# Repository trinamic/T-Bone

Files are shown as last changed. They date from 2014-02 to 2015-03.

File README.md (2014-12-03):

T-Bone
======
Electronic for up to 5 axes DIY desktop manufacturing platforms

LICENSE Files
=============
"LICENSE_HW" --> Attribution-ShareAlike 4.0 International license effective for the hardware part
"LICENSE_SW" --> agpl-3.0 license effective for the software part

"Software/ArduinoClient" Folder
===============================
The ArduinoClient folder  contains the Arduino software.

"Documentation/SoftwareDocumentation.pdf" File
==============================================
Documentation for the implemented protocol to communicate with the T-Bone via the UART interface.

"Documentation/T-bone_command_documentation.txt" File
=====================================================
Example file for the communication between Beagle Bone Black and the T-Bone (Arduino Leonardo)

Arduino Leonardo Pinout
=======================
Adapted from pins.h in the Arduino software.

Arduino Pin – Atmel Pin & function - connection

    D0 - PD2, RXD1/INT2 - Serial BeagleBone (UART1_TXD)
    D1 - PD3 TXD1/INT3 - Serial BeagleBone (UART1_RXD)
    D2 - PD1 SDA SDA/INT1 - Interrupt 4361 Nr.2
    D3# - PD0 PWM8/SCL OC0B/SCL/INT0 - Interrupt 4361 Nr.1
    D4 - A6 - PD4 ADC8 - CS 4361 Nr. 1
    D5# - PC6 ??? OC3A/#OC4A - PWM3, Fan
    D6# A7 - PD7 FastPWM #OC4D/ADC10 - CS 5031 Nr. 3
    D7 - PE6 INT6/AIN0 - Interrupt 4361 Nr.3
    D8 A8 - PB4 ADC11/PCINT4 - Interrupt 5041
    D9# A9 - PB5 PWM16 OC1A/#OC4B/ADC12/PCINT5 - PWM 1
    D10# A10 - PB6 PWM16 OC1B/0c4B/ADC13/PCINT6 - PWM 2
    D11# - PB7 PWM8/16 0C0A/OC1C/#RTS/PCINT7 - CS 5041
    D12 A11 - PD6 T1/#OC4D/ADC9 - CS 4361 Nr. 2
    D13# - PC7 PWM10 CLK0/OC4A - clock output do not use, never!
    A0 - D18 PF7 ADC7 - Temperature Sensor 1
    A1 - D19 PF6 ADC6 - Temperature Sensor 2
    A2 - D20 PF5 ADC5 - Temperature Sensor 3
    A3 - D21 PF4 ADC4 - Start Signal
    A4 - D22 PF1 ADC1 - Current PWM 1
    A5 - D23 PF0 ADC0 - Current PWM 2
    MISO - D14 PB3 MISO,PCINT3 - MISO
    SCK - D15 PB1 SCK,PCINT1 - SCK
    MOSI - D16 PB2 MOSI,PCINT2 - MOSI
    SS - D17 PB0 RXLED,SS/PCINT0 - RX LED
    TXLED - PD5 . TX LED
    HWB - PE2 HWB - Reset for motion drivers

"Software/ArduinoLibraries" Folder
==================================
This folder contains the used Arduino Libraries needed to compile the code.
!!Attention!!
The used libraries are standard ones, BUT customized. So be sure to use these!
!!Attention!!

For information on installing libraries, see: http://arduino.cc/en/Guide/Libraries

"Software/t_bone_server" Folder
===============================
This folder contains the software running on the Beagle Bone Black for the Deluxe version.

It's prepared to run a 3D-Printer Hardware. But can be customized to control different kind of desktop manufacturing platforms.

"Hardware/T-Bone Folder"
========================
Contains schematic and board design of the latest version of the T-Bone HW

"Hardware/Programming board" Folder
===================================
Contains schematic of a programming board adapter

"Hardware/BBQ" Folder
=====================
Contains schematic and board design for BBQ breakout board to evaluate TMC chipsets

"Hardware/TMC2100" Folder
=========================
Contains startup instructions for TMC2100 breakout board and schematics + board design

LJ

The T-Bone Team
2014

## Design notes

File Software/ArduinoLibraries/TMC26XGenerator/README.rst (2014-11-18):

Arduino TMC26X Stepper Motor Controller Library
===============================================

License
-------

TMC26XStepper.cpp - - TMC 260/261/262 Stepper library for Wiring/Arduino
 
based on the stepper library by Tom Igoe, et. al.
 
Copyright (c) 2011, Interactive Matter, Marcus Nowotny
 
Permission is hereby granted, free of charge, to any person obtaining a copy
of this software and associated documentation files (the "Software"), to deal
in the Software without restriction, including without limitation the rights
to use, copy, modify, merge, publish, distribute, sublicense, and/or sell
copies of the Software, and to permit persons to whom the Software is
furnished to do so, subject to the following conditions:
 
The above copyright notice and this permission notice shall be included in
all copies or substantial portions of the Software.
 
THE SOFTWARE IS PROVIDED "AS IS", WITHOUT WARRANTY OF ANY KIND, EXPRESS OR
IMPLIED, INCLUDING BUT NOT LIMITED TO THE WARRANTIES OF MERCHANTABILITY,
FITNESS FOR A PARTICULAR PURPOSE AND NONINFRINGEMENT. IN NO EVENT SHALL THE
AUTHORS OR COPYRIGHT HOLDERS BE LIABLE FOR ANY CLAIM, DAMAGES OR OTHER
LIABILITY, WHETHER IN AN ACTION OF CONTRACT, TORT OR OTHERWISE, ARISING FROM,
OUT OF OR IN CONNECTION WITH THE SOFTWARE OR THE USE OR OTHER DEALINGS IN
THE SOFTWARE.

About
-----

The TMC26X is a stepper motor controller for bipolar stepper motors. From the trinamic web site:

 The TMC262 is the first energy efficient high current high precision microstepping driver 
 IC for bipolar stepper motors. The unique high resolution sensorless load detection stallGuard2™ 
 is used to for the world’s first integrated load dependent current control feature called coolStep™.
 The ability to read out the load and detect an overload makes the TMC262 an optimum choice for 
 drives where a high reliability is desired at a low cost. The new patented spreadCycle PWM mixed 
 decay chopper scheme ensures best zero crossing performance as well as high speed operation. 
 The TMC262 can be driven with Step & Direction signals as well as by serial SPI™ interface. 
 Using the microPlyer allows to operate the motor with highest 256 μStep smoothness reducing the 
 input frequency to 16 μSteps. A full set of protection and diagnostic features makes this device 
 very rugged. It directly drives external MOSFETs for currents of up to 6A. This way it reaches 
 highest energy efficiency and allows driving of a high motor current without cooling measures 
 even at high environment temperatures.

The unique features of the TMC26X are that everything can (and must) be controlled in software:

* the motor current
* microstepping
* stall protection
* current reduction according to load
* stallGuard2™ sensorless load detection
* coolStep™ load dependent current control
* spreadCycle hysteresis PWM chopper 
* microPlyer 16-to-256 μStep multiplier
* full protection and diagnostics

This makes the TMC26X a bit harder to use than other stepper motors but much more versatile.
This library resolves all the complicated stuff so that you can use TMC26X straight away.
Furthermore, all the settings are implemented in high level interfaces so that configuring your
motor is a breeze.

How to use
----------

Check out the Setup Guide here: 
And the How To here:

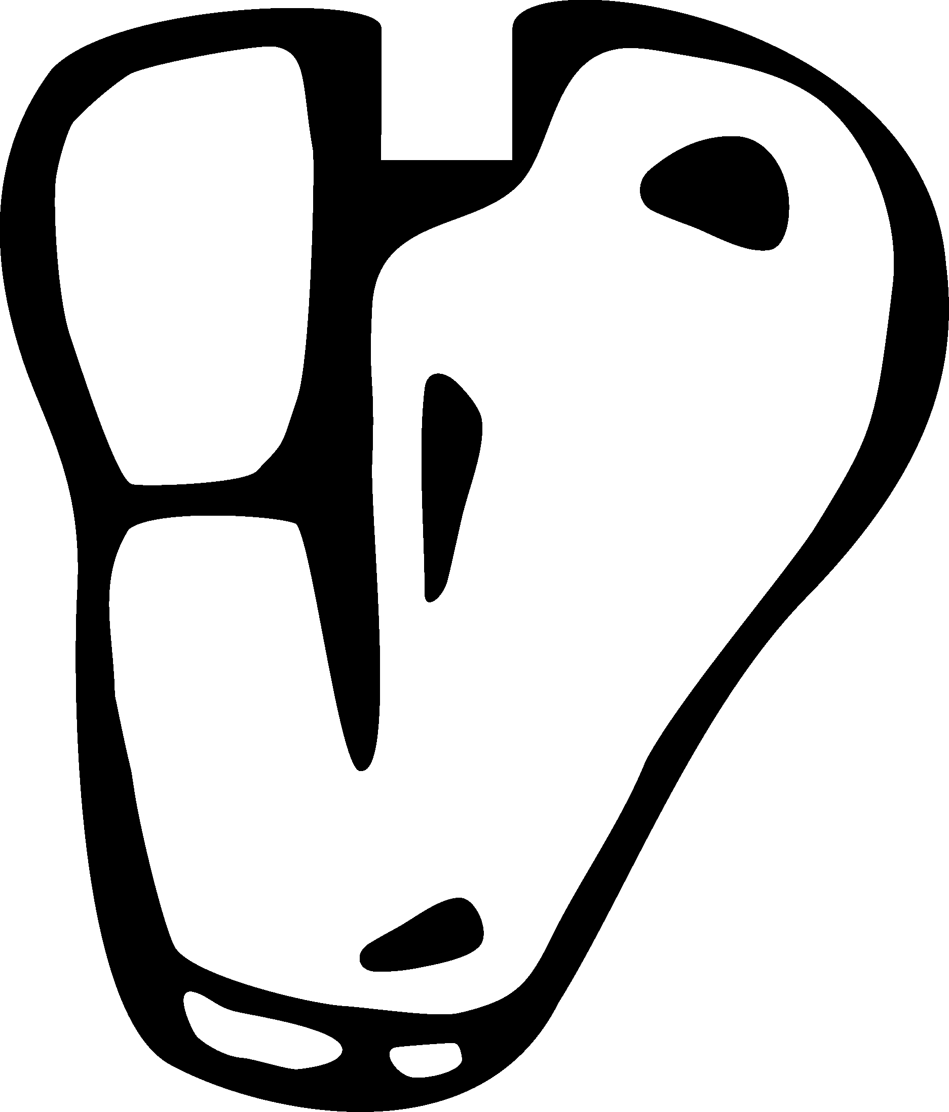
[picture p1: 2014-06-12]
Hardware/Others/T-Bone silkscreen/slikskreen.bmp

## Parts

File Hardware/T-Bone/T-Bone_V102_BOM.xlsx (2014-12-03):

LJ |  |  | T-Bone_v102_BOM | 2014-09-17
Ref. | Qty | Option | Description | digiKey part | Package | URL
C209 | 1 |  | 0805 100nF/25V | GRM21BR71E104KA01K | 0805 | http://www.digikey.com/product-detail/en/GRM21BR71E104KA01L/490-1673-2-ND/586699
C204 | 1 |  | 1206 1µF/50V | C3216X7R1H105K | 1206 | http://www.digikey.com/product-detail/en/C3216X7R1H105K160AB/445-1423-2-ND/569049
C208 | 1 |  | 0805 1µF/35V | GMK212B7105KG-T | 0805 | http://www.digikey.com/product-detail/en/GMK212B7105KG-T/587-1438-2-ND/1004026
C210 | 1 |  | 0603 10µF/50V | GRM188R60J106ME47D | 0603 | http://www.digikey.com/product-detail/en/GRM188R60J106ME47D/490-3896-2-ND/965910
C207 | 1 |  | 0805 10nF/50V | GRM216R71H103KA01D | 0805 | http://www.digikey.com/product-detail/en/GRM216R71H103KA01D/490-1664-2-ND/586759
D202 | 1 |  | SMA Diode | B240A-13-F | SMA | http://www.digikey.com/product-detail/en/B240A-13-F/B240A-FDITR-ND/717691
L201 | 1 |  | SDR0805 Spule 12µH/2A | SDR0805-120ML | SDR0805 | http://www.digikey.com/product-detail/en/SDR0805-120ML/SDR0805-120MLTR-ND/1970437
R204 | 1 |  | 0402 10kOhm/1% | CRCW040210K0FKED | 0402 | http://www.digikey.com/product-detail/en/CRCW040210K0FKED/541-10.0KLTR-ND/1178121
R203 | 1 |  | 0402 9.76kOhm/1% | CRCW04029K76FKED | 0402 | http://www.digikey.com/product-detail/en/CRCW04029K76FKED/541-9.76KLTR-ND/1178120
R202 | 1 |  | 1210 110mOhm/1% | MCR25JZHFLR110 | 1210 | http://www.digikey.com/product-detail/en/MCR25JZHFLR110/RHM.11STR-ND/1852936
R201 | 1 |  | 0402 140kOhm/1% | CRCW0402140KFKED | 0402 | http://www.digikey.com/product-detail/en/CRCW0402140KFKED/541-140KLTR-ND/1178250
IC | 1 |  | Schaltregler | LM25011MY/NOPB | 10-MSOP/MUC10A | http://www.digikey.com/product-detail/en/LM25011MY%2FNOPB/LM25011MY%2FNOPBTR-ND/2080162
F201 | 2 | MEDIUM | Fuse holder | F4186-ND | non standard | http://www.digikey.de/product-detail/de/01000058Z/F4186-ND/2518627
- | 1 |  | Fuse for Fuse holder F201 | 0AGW015.V | 1/4" x 7/8" | http://www.digikey.de/product-detail/de/0AGW015.V/F5032-ND/2519086
D201 | 1 |  | Schottky Diode | SMBJ28A | DO-214AA, SMB | http://www.digikey.com/product-detail/en/SMBJ28A/SMBJ28ALFCT-ND/286109
C203 | 1 |  | 100µF/35V LowESR | EEE-FK1V101P | Size code: F | http://www.digikey.com/product-detail/en/EEE-FK1V101P/PCE3835CT-ND/766211
IC201 | 1 |  | Switching Regulator | LD1117S33TR | SOT223 | http://www.digikey.com/product-detail/en/LD1117S33TR/497-1242-1-ND/586242
C201 / C206 | 2 |  | Kondensator 0805 10µF/10V | CC0805ZKY5V6BB106 | 0805 | http://www.digikey.com/product-detail/en/CC0805ZKY5V6BB106/311-1355-1-ND/2103139
C202 / C205 | 2 |  | 0603 100nF/50V | CC0603ZRY5V9BB104 | 0603 | http://www.digikey.com/product-detail/en/CC0603ZRY5V9BB104/311-1343-1-ND/2103127
IC101 | 1 |  | EEPROM | CAT24C256WI-GT3OSCT-ND | SO8 | http://www.digikey.com/product-detail/en/CAT24C256WI-GT3/CAT24C256WI-GT3OSCT-ND/2704982
R101 - R103 | 3 |  | 0402 4k7 | RC0402FR-074K7L | 0402 | http://www.digikey.com/product-detail/en/RC0402FR-074K7L/311-4.7KLRTR-ND/2827563
R107 | 2 |  | 0402 5k6 | RC0402FR-075K62L | 0402 | http://www.digikey.com/product-detail/en/RC0402FR-075K62L/311-5.62KLRTR-ND/726627
C101 | 1 |  | 0402 100nF/10V | CC0402KRX5R6BB104 | 0402 | http://www.digikey.com/product-detail/en/CC0402KRX5R6BB104/311-1336-1-ND/2103120
P8 / P9 | 2 | MEDIUM | 2x23 | Pinheader 2x23 | 2.54mm | http://www.digikey.com/product-detail/en/SSQ-123-03-T-D/SAM1204-23-ND/1111837
IC301 | 1 |  | Atmega 32u4 | ATMEGA32U4-MU | 44QFN | http://www.digikey.com/product-detail/en/ATMEGA32U4-MU/ATMEGA32U4-MU-ND/1914603
X1 | 1 |  | Mini USB-Anschlussbuchse | ED2992DKR-ND | - | http://www.digikey.com/product-detail/en/USB-M26FTR/ED2992DKR-ND/2677757
R301 / R302 | 2 |  | 0402 22R,1% | RC0402FR-0722RL | 0402 | http://www.digikey.com/product-detail/en/RC0402FR-0722RL/311-22.0LRTR-ND/726562
U$301 | 1 |  | Reset Taster | FSM4JSMATR | 6mm x 6mm | http://www.digikey.com/product-detail/en/FSM4JSMATR/450-1759-1-ND/2271638
R303 / R304 | 2 |  | 0603 10k, 5% | RMCF0603JG10K0 | 0603 | http://www.digikey.com/product-detail/en/RMCF0603JG10K0/RMCF0603JG10K0CT-ND/4425128
Q301 | 1 |  | Quarz 16MHz | ECS-160-20-5PX-TR | HC49/US | http://www.digikey.com/product-detail/en/ECS-160-20-5PX-TR/XC1282CT-ND/827746
C301 / C302 | 2 |  | 0603 22pF/50V | C1608C0G1H220J080AA | 0603 | http://www.digikey.com/product-detail/en/C1608C0G1H220J080AA/445-1273-2-ND/513755
C303 / C305 | 2 |  | 0603 1µF/50V | UMK107BJ105KA-T | 0603 | http://www.digikey.com/product-detail/en/UMK107BJ105KA-T/587-2400-1-ND/2179013
C304 | 1 |  | 0603 100nF/50V | CC0603ZRY5V9BB104 | 0603 | http://www.digikey.com/product-detail/en/CC0603ZRY5V9BB104/311-1343-1-ND/2103127
L301 | 1 |  | 0805 Ferrite Bead | MH2029-300YTR-ND | 0805 | http://www.digikey.com/product-detail/en/MH2029-300Y/MH2029-300YTR-ND/2563323
F301 | 1 |  | 1812 Sicherung 500mA | MF-MSMF050-2 | 1812 | http://www.digikey.com/product-detail/en/MF-MSMF050-2/MF-MSMF050-2TR-ND/662816
IC302 | 1 |  | Hex high-to-low level shifter | SN74LVC04ARGYR | 14VQFN | http://www.digikey.com/product-detail/en/SN74LVC04ARGYR/296-13956-1-ND/521533
RN301 | 1 |  | 100R0, 5% 4er Array | YC124-JR-07100RL | 0804 | http://www.digikey.com/product-detail/en/YC124-JR-07100RL/YC124J-100CT-ND/1005529
IC401 | 1 |  | Motion Controller + Driver | TMC5041 | QFN48 | TRINAMIC
C402 / C405 | 2 |  | 0603 22nF/50V | C1608X7R1H223K080AA | 0603 | http://www.digikey.com/product-detail/en/C1608X7R1H223K080AA/445-1312-1-ND/567696
C406 / C409 / C410 / C401 | 4 |  | 0603 100nF/50V | CC0603ZRY5V9BB104 | 0603 | http://www.digikey.com/product-detail/en/CC0603ZRY5V9BB104/311-1343-2-ND/2103081
C407 / C408 | 2 |  | 220µF/35V | EEE-FK1V221P | Size code: F | http://www.digikey.com/product-detail/en/EEE-FK1V221P/PCE3839CT-ND/766215
R404 / R405 / R406 / R407 | 4 |  | 1206 0R27/0.5W | RL1206FR-070R27L | 1206 | http://www.digikey.com/product-detail/en/RL1206FR-070R27L/311-.27LWCT-ND/3886097
C403 | 1 |  | 0603 470nF/16V | C1608X7R1C474K080AC | 0603 | http://www.digikey.com/product-detail/en/C1608X7R1C474K080AC/445-5192-1-ND/2093807
C404 | 1 |  | 0603 4,7µF/16V | EMK107ABJ475KA-T | 0603 | http://www.digikey.com/product-detail/en/EMK107ABJ475KA-T/587-2786-1-ND/2573980
R403 | 1 |  | 0603 2R2/1% | RC0603FR-072R2L | 0603 | http://www.digikey.com/product-detail/en/RC0603FR-072R2L/311-2.2HRCT-ND/2827910
R402 | 1 |  | 0603 1k/1% | RMCF0603FT1K00 | 0603 | http://www.digikey.com/product-detail/en/RMCF0603FT1K00/RMCF0603FT1K00CT-ND/1942996
R401 | 1 |  | 0603 2k/1% | RC0603FR-072K2L | 0603 | http://www.digikey.com/product-detail/en/RC0603FR-072K2L/311-2.20KHRCT-ND/729963
D401 | 1 |  | MSS1P6 | MSS1P6-M3/89A | MSS1Px | TRINAMIC
IC501 / IC601 / IC701 | 3 |  | Motion Controller | TMC4361 | QFN40L | TRINAMIC
C501 / C502 / C503 / C504 / C505 / C601 / C602 / C603 / C604 / C605 / C701 / C702 / C703 / C704 / C705 | 15 |  | 0603 100nF/50V | CC0603ZRY5V9BB104 | 0603 | http://www.digikey.com/product-detail/en/CC0603ZRY5V9BB104/311-1343-2-ND/2103081
IC502 / IC602 / IC702 | 3 |  | Motor Driver | TMC2660 | PQFP44_WITH_PADS | TRINAMIC
C512 / C612 / C712 | 3 |  | 220µF/35V | EEE-FK1V221P | Size code: F | http://www.digikey.com/product-detail/en/EEE-FK1V221P/PCE3839CT-ND/766215
C506 / C606 / C706 | 3 |  | 0603 220nF/16V | C1608X7R1C224K080AC | 0603 | http://www.digikey.com/product-detail/en/C1608X7R1C224K080AC/445-1318-1-ND/567690
C507 / C508 / C607 / C608 / C707 / C708 | 6 |  | 1210 10µF/35V | GMK325F106ZH-T | 1210 | http://www.digikey.com/product-detail/en/GMK325F106ZH-T/587-1391-1-ND/931168
R504 / R505 / R604 / R605 / R704 / R705 | 6 |  | 0603 10R | ERJ-3EKF10R0V | 0603 | http://www.digikey.com/product-detail/en/ERJ-3EKF10R0V/P10.0HCT-ND/198100
R506 / R507 / R606 / R607 / R706 / R707 | 6 |  | 1206 0R10/0.5W | LR1206-R10FW | 1206 | http://www.digikey.com/product-detail/en/LR1206-R10FW/985-1191-1-ND/2402033
C509 / C510 / C609 / C610 / C709 / C710 | 6 |  | 0603 100nF/50V | CC0603ZRY5V9BB104 | 0603 | http://www.digikey.com/product-detail/en/CC0603ZRY5V9BB104/311-1343-2-ND/2103081
C511 / C611 / C711 | 3 |  | 0603 470nF/16V | C1608X7R1C474K080AC | 0603 | http://www.digikey.com/product-detail/en/C1608X7R1C474K080AC/445-5192-1-ND/2093807
R501 / R502 / R503 / R601 / R602 / R603 / R701 / R702 / R703 | 9 |  | 0603 4k7/1% | RC0603FR-074K7L | 0603 | http://www.digikey.com/product-detail/en/RC0603FR-074K7L/311-4.70KHRCT-ND/730159
U$501 / U$601 / U$701 | 3 |  | Triple Schmitt Trigger Buffer | SN74LVC3G17DCTR | SM8 | http://www.digikey.com/product-detail/en/SN74LVC3G17DCTR/296-16915-2-ND/644202
R551 / R651 / R751 / R471 / R550 / R650 / R450 / R750 / R470 / R561 / R661 / R461 / R761 / R481 / R560 / R660 / R460 / R760 / R480 / R451 | 20 |  | 0402 4k7/1% | RC0402FR-074K7L | 0402 | http://www.digikey.com/product-detail/en/RC0402FR-074K7L/311-4.7KLRTR-ND/2827563
R901 / R903 / R905 | 3 |  | 0402 4k7/1% | RC0402FR-074K7L | 0402 | http://www.digikey.com/product-detail/en/RC0402FR-074K7L/311-4.7KLRTR-ND/2827563
C901 - C906 | 6 |  | 0402 470nF/50V | C0402C473K9PACTU | 0402 | http://www.digikey.com/product-detail/en/C0402C473K9PACTU/399-3020-1-ND/447598
R902 / R904 / R906 | 3 |  | 0402 6k8/1% | RC0402FR-076K8L | 0402 | http://www.digikey.com/product-detail/en/RC0402FR-076K8L/311-6.80KLRCT-ND/729589
Q802 / Q803 | 2 |  | FET BSS138 | BSS138 | SOT23 | http://www.digikey.com/product-detail/en/BSS138/BSS138CT-ND/244294
IC801 / IC804 | 2 |  | Power switch FDDS10H04A_F085A | FDDS10H04A_F085A | PG-TO252-5-11 | http://www.digikey.com/product-detail/en/FDDS10H04A_F085A/FDDS10H04A_F085ACT-ND/4494084
C801 / C803 | 2 |  | 10µF/50V | EEE-FC1H100P | Size code: D | http://www.digikey.com/product-detail/en/EEE-FC1H100P/PCE4012CT-ND/817474
C802 / C804 | 2 |  | 0805 100nF/50V | CC0805ZRY5V9BB104 | 0805 | http://www.digikey.com/product-detail/en/CC0805ZRY5V9BB104/311-1361-1-ND/2103145
R804 / R810 | 2 |  | 0603 180R/1% | RC0603FR-07180RL | 0603 | http://www.digikey.com/product-detail/en/RC0603FR-07180RL/311-180HRTR-ND/726994
R807 / R813 | 2 |  | 0603 1k2/1% | RC0603FR-071K2L | 0603 | http://www.digikey.com/product-detail/en/RC0603FR-071K2L/311-1.20KHRCT-ND/729799
R806 / R812 | 2 |  | 0603 10k/1% | RC0603FR-0710KL | 0603 | http://www.digikey.com/product-detail/en/RC0603FR-0710KL/311-10.0KHRTR-ND/726880
R805 / R811 | 2 |  | 0603 1k/1% | RC0603FR-071KL | 0603 | http://www.digikey.com/product-detail/en/RC0603FR-071KL/311-1.00KHRCT-ND/729790
D802 / D804 | 2 |  | SMBJ36CA | SMBJ36CA | SMB/DO-214AA | http://www.digikey.com/product-detail/en/SMBJ36CA/SMBJ36CAFSCT-ND/2094452
R803 / R809 | 2 | MEDIUM | Disk Varistor (S10K35) | S10K35 | 7.5mm RM | http://www.digikey.com/product-detail/en/S10K35/495-2400-ND/651303
D803 / D805 | 2 |  | Zener Diode | MMSZ4678-TP | SOD-123 | http://www.digikey.com/product-detail/en/MMSZ4678-TP/MMSZ4678-TPMSCT-ND/4080530
Q801 | 1 |  | Self protected FET | AO7400 | SOT323 | http://www.digikey.com/product-detail/en/AO7400/785-1084-2-ND/1855856
D801 | 1 |  | Diode | CGRA4001-G |  | http://www.digikey.com/product-detail/en/CGRA4001-G/641-1016-2-ND/1121048
R801 / R802 / R808 | 3 |  | 0603 12k0/1% | RC0603FR-0712KL | 0603 | http://www.digikey.com/product-detail/en/RC0603FR-0712KL/311-12.0KHRCT-ND/729860
LED2_BB / LED3_BB / LED4_BB / RX_LED | 4 |  | TLMY-1000 | TLMS1000-GS08 | 0603 | http://www.digikey.com/product-detail/en/TLMS1000-GS08/TLMS1000-GS08-ND/4075818
LED1_BB / POWER_LED | 2 |  | TLMS-1000 | TLMY1000-GS08 | 0603 | http://www.digikey.com/product-detail/en/TLMY1000-GS08/TLMY1000-GS08-ND/4075819
TX_LED / FAN_LED / PWM1_LED / PWM2_LED / END1L_LED / END2L_LED / END3L_LED / END4L_LED / END5L_LED / END1R_LED / END2R_LED / END3R_LED / END4R_LED / END5R_LED | 14 |  | TLMO-1000 | TLMO1000-GS08 | 0603 | http://www.digikey.com/product-detail/en/TLMO1000-GS08/TLMO1000-GS08-ND/4075858
R2 / R106 / R108 | 3 |  | 0402 1k0, 5% | RMCF0402JT1K00 | 0402 | http://www.digikey.com/product-detail/en/RMCF0402JT1K00/RMCF0402JT1K00DKR-ND/1943840
R552 / R652 / R452 / R752 / R472 / R562 / R662 / R462 / R762 / R482 | 10 |  | 0402 10k0, 5% | RMCF0402JT10K0CT-ND |  | http://www.digikey.com/product-detail/en/RMCF0402JT10K0/RMCF0402JT10K0CT-ND/1942936
RN101 | 1 |  | 1k0, 5% 4er Array | YC124-JR-071KL | 804 | http://www.digikey.com/product-detail/en/YC124-JR-071KL/YC124J-1.0KTR-ND/1004996
X201 | 1 | MEDIUM | Stecker 4 polig Power supply | 1757268 | - | http://www.digikey.com/product-detail/en/1757268/277-1108-ND/260476
IC802 | 1 |  | OR-Gatter | SN74LVC32ARGYR | 14VQFN | http://www.digikey.com/product-detail/en/SN74LVC32ARGYR/296-13819-1-ND/513496
IC803 | 1 |  | NOR-Gatter | SN74LVC02ARGYR | 14VQFN | http://www.digikey.com/product-detail/en/SN74LVC02ARGYR/296-13955-1-ND/521531
X801 / X802 | 2 | MEDIUM | 2polig (bis 12A) | WM7845-ND | - | http://www.digikey.com/product-search/en?vendor=0&keywords=WM7845-ND
J801 / J902 / J904 / J907 | 4 | MEDIUM | 2polig TE-Connectivity | 640455-2 | - | http://www.digikey.com/product-detail/en/640455-2/A19450-ND/258997
J101 / J550 / J650 / J450 / J750 / J470 / J560 / J660 / J460 / J760 / J480 | 11 | MEDIUM | 3polig TE-Connectivity | 640455-3 | - | http://www.digikey.com/product-detail/en/640455-3/A19451-ND/258998
J401 / J402 / J502 / J602 / J702 | 5 | MEDIUM | 4polig TE-Connectivity | 640455-4 | - | http://www.digikey.com/product-detail/en/640455-4/A19452-ND/258999
J501 / J601 / J701 | 3 | MEDIUM | 5polig TE-Connectivity | 640455-5 | - | http://www.digikey.com/product-detail/en/640455-5/A19453-ND/259000
R1 | 1 |  | 0402 2k2, 1% | 311-2.20KLRCT-ND | 0402 | http://www.digikey.com/product-detail/en/RC0402FR-072K2L/311-2.20KLRCT-ND/729500
 | 253

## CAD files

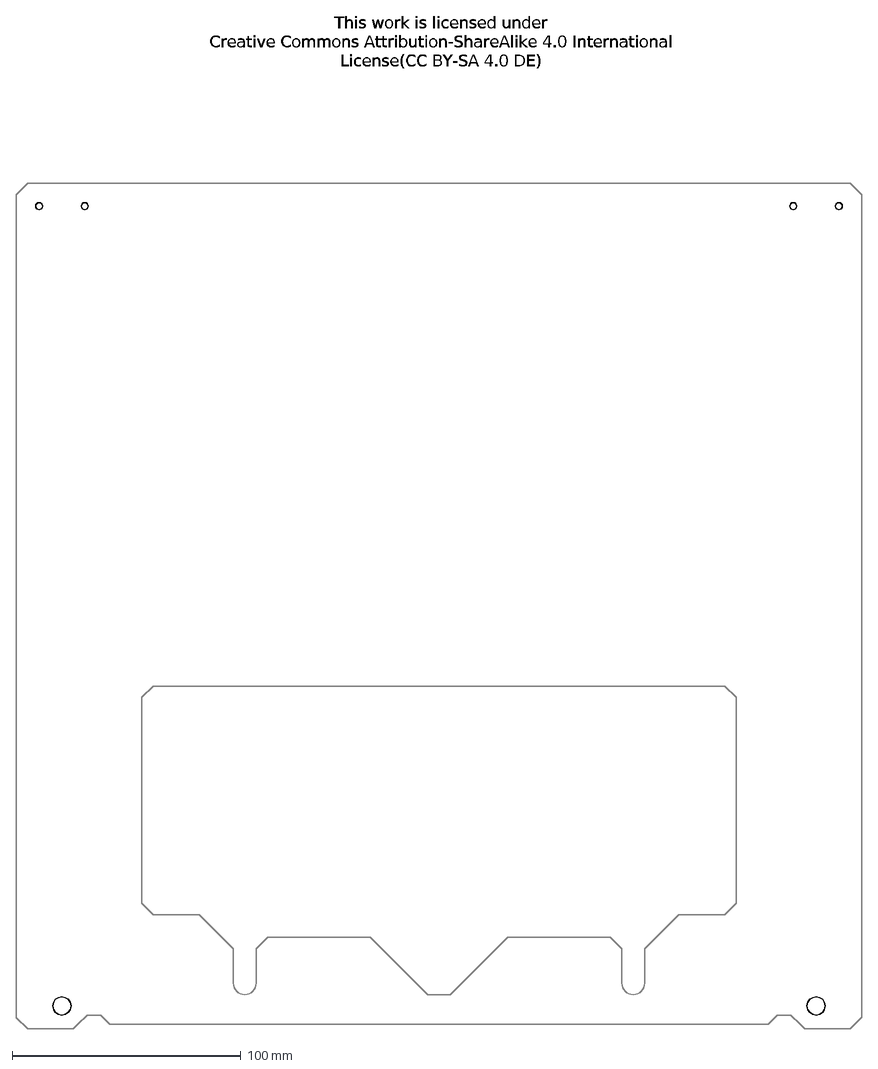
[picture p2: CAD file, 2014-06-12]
Hardware/Others/Prusa I3 plexiglass bracket/Prusa T-Bone Holder.dxf
This work is licensed under Creative Commons Attribution-ShareAlike 4.0 International License (CC BY-SA 4.0 DE)

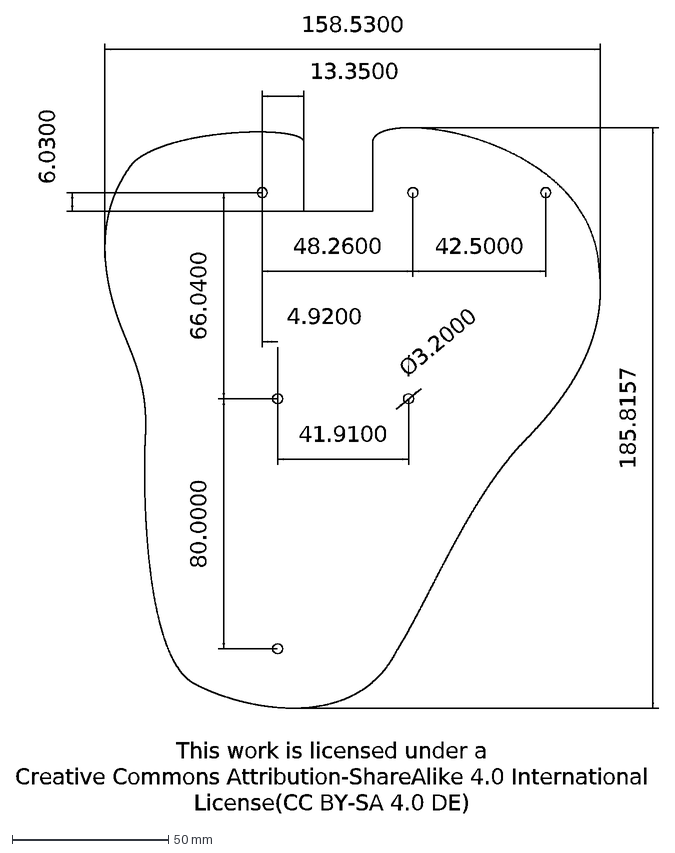
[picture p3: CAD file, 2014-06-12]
Hardware/Others/T-Bone technical drawing/T-Bone.dxf
This work is licensed under a Creative Commons Attribution-ShareAlike 4.0 International License (CC BY-SA 4.0 DE)
185.8157
48.2600
42.5000
66.0400
80.0000
41.9100
4.9200
6.0300
13.3500
158.5300
Ø3.2000

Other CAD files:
Hardware/Others/T-Bone silkscreen/tbonoid-slikscreen.dxf
Hardware/Others/Prusa I3 plexiglass bracket/Prusa T-Bone Holder.skp

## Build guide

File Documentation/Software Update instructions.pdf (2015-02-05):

# Update instruction

To update the software for the T-Bone, please do the following steps

1. Download the Arduino IDE (http://arduino.cc/en/Main/Software)
2. Download the latest T-Bone Software (https://github.com/trinamic/T-Bone/tree/master/Software/ArduinoClient) (https://github.com/trinamic/T-Bone/tree/master/Software/ArduinoClient)
3. Download all libraries (https://github.com/trinamic/T-Bone/tree/master/Software/ArduinoLibraries) (https://github.com/trinamic/T-Bone/tree/master/Software/ArduinoLibraries)
4. Copy libraries to: C:\Users\Username\Documents\Arduino\libraries
a. If folder does not exist, create it
5. Open Arduino IDE
6. Open “ArduinoClient.ino”
7. Power up T-Bone
8. Connect T-Bone via USB to computer
9. Select the right Serial Port
10. Upload the Code
11. Done

To update the Beagle Bone Black software, please do these steps:

1. Connect Beagle Bone Black (BBB) with power
2. Connect BBB with Internet
3. Connect to BBB via SSH, e.g. with putty (http://www.putty.org/)
4. Username: root Password: none (just hit ENTER)
5. Go to directory “/home/root/trinamic3d/”
6. Type in: “git pull”
7. Wait until download complete
8. Done

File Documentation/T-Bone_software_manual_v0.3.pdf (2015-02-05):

Hardware to control desktop manufacturing plattforms | T-Bone

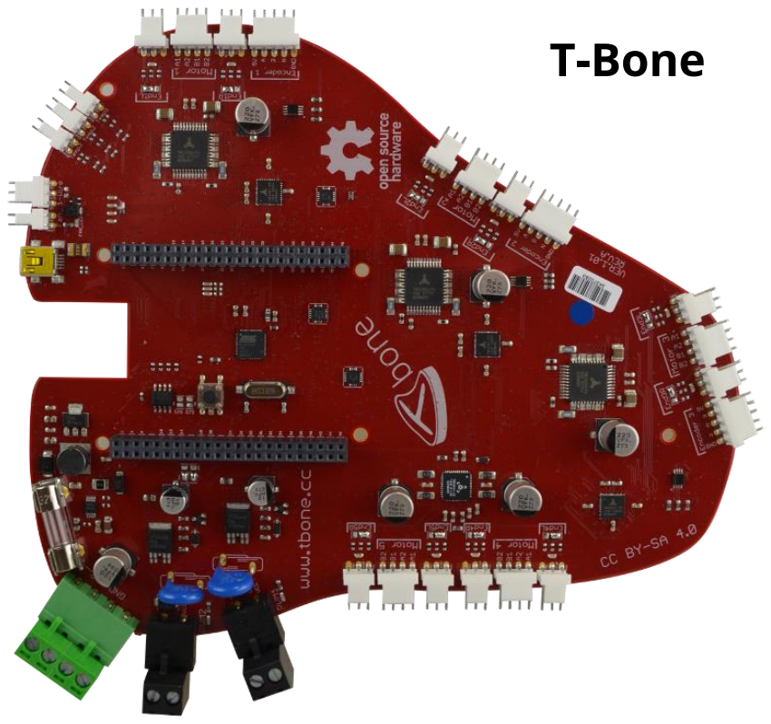
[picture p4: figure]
T-Bone
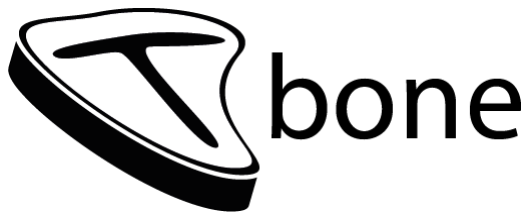
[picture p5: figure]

T-Bone Team
Hamburg, Germany

www.tbone.cc

V 0.3

# SOFTWARE MANUAL

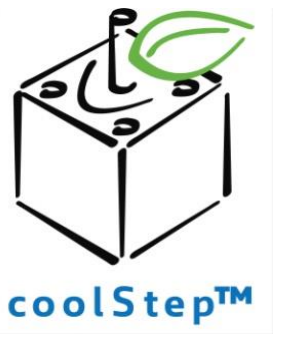
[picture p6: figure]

T-Bone Software Manual (V0.3 / 2015-FEB-5) | 2

T-Bone Team

# Table of contents

# 1 License

The T-Bone software is published under the GNU AFFERO GENERAL PUBLIC LICENSE [agpl-3.0]

T-Bone Team 2014

# 2 Base Architecture

The idea of the T-Bone software architecture is to use to reduce the real time requirements for the motion control part and implement that in a high level language (here python). To achieve this the motions of the squirrel motion controller are used as timings.

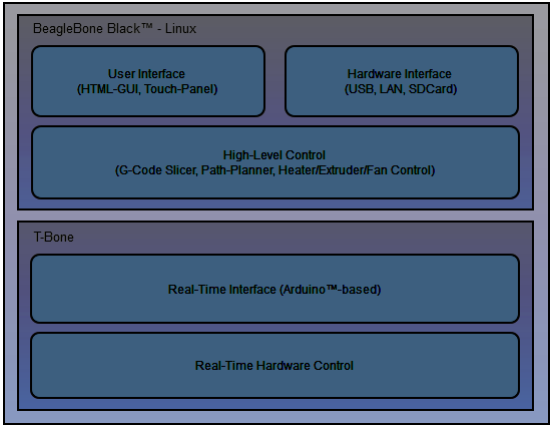
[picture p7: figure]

Figure 1 - Base Architecture

The BeagleBone is used as User Interface provider and high level path and motion planner, while the Arduino Leonardo is used as Real Time Interface to translate between the high level concepts of the T-Bone python part and the hardware.
The architecture is a pipe and filter architecture, containing several buffers which are kept at a certain level to make the different software parts independent from each other in timing. By thish slight timing variations can be easily compensated.

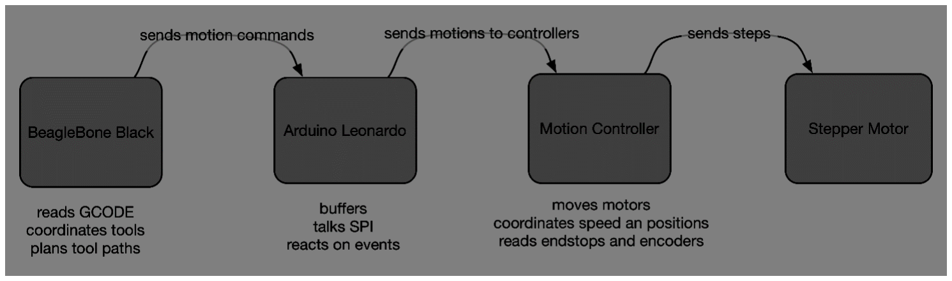
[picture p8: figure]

The Python Code on the Beagle Bone reads the GCODE, interprets and recalculates the movement (e.g. from inches to mm). The BeagleBone also hosts the web interface and contains the server part. During GCODE interpretation it also applies motion planning over several segments of a motion.
The Arduino Leonardo keeps a planned motion buffer and coordinates it's execution in the motion controllers. It also hides details of the squirrel programming from the python part. The Arduino Leonardo is connected by serial connection to the python part and by SPI to the squirrel motion controllers.
The motion controllers itself know just two motions: the currently executed motion and the next motion to execute and coordinate the stepper motor.

Figure 2 - Toolchain

# 3 Software Modules of the Python Server

## 3.1 The T-Bone Server

The module 't_bone_server.py' – especially contain the command line interface to start the server (in the main routine) and the service endpoints for the web interface (the controllers in a model-view-controller
architecture). | The | web | interface | itself | is | rendered | with | the | HTML | templates | in
't_bone_server/src/t_bone/templates' containing a base template (base.html) with all the header and footer information which are the same for all pages. The pages itself are realized as sub templates.
The web server itself does not have any logic to interpret GCODE or configure the 3D printer itself.

## 3.2 The 3D Printer

The module 'printer.py' contain the high level abstraction of the reprap 3D Printer. It knows is axis, it knows how to read the configuration. It knows that the axis correspond to motors. It translates between real world coordinates in millimetres and stepper motor coordinates in steps. It knows that a path to move consist of several parts and that you do not have to stop at the end of each segment.
The 'Printer' is it's own thread which coordinates the movements itself. The configuration is done by handing a dictionary (or JSON file) to the configure() routine. This routine interprets the information and sets the member variables of the printer and axis accordingly.

A print is started with 'start_print()', the several movements can be added with 'move_to()' and in the end the print is finished with 'finish_print()'. The print buffer is split in two separate buffers: The planning buffer in the class 'PrintQueue' (as member variable _print_queue). This planning buffer has a fixed length and is used for motion and path planning. If an move is added to the print queue with 'add_movement()' four steps are performed:
- the maximum achievable speed for the move is calculated. Depending on the speed and direction of the previous move and the motion parameter configuration the print head can be further accelerated or must stop and accelerate from 0.
- It can be decided if there is a stop for an axis in the previous move or the motor can just move on. After this the configuration of the previous move is finished and the previous move can be added to the planning list in 'planning_list'.
- If the planning list is long enough the first move is removed and pushed to the execution list in _push_from_planning_to_execution().
- After this all moves in the planning list are recalculated in _recalculate_move_speeds() to check if we work from the back of the planning list to the front of the planning list we can brake fast enough to achieve the target speeds of each move. If the achievable speed is higher than the highest possible brake speed it must be reduced.

The execution list in 'queue' is a simple Queue with a maximum length which is used by two separate Threads:
- The printer pushed executable movements to the queue
- The print queue reads executable moves and executes it on the machine (see next paragraph) if there is enough space in the Arduino Leonardo internal execution queue

## 3.3 The GCODE Interpreter

For simplicity reasons the GCODE interpreter itself is kept in the 'gcode_interpreter.py' module. It contains logic to read from machine specific GCODE to the API of the 3D Printer. There is no direct connection between the 3D Printer and the GCODE to allow easy adaption and change of GCODE interpretation.

## 3.4 The low level Machine Interface

The module 'machine.py' contains the serial communication interface to the Arduino Leonardo. It is a separate Thread which ends requests, receives and decodes answers and is also notified by heartbeat pings from the Arduino Leonardo to update status information. It translates between the object language of the printer and the technical language of the serial communication.

## 3.5 The Heater

The module 'heater.py' contains the logic to keep a heater at a constant temperature. A heater consist of a thermistor and a PWM output. The heating logic can either be a PID controller (for the Hotend) or a simple two point controller (for the heated bed). The Thermistor logic is separated in the 'thermistor.py', 'replicpe_thermistors.py' and 'ramps_thermistors.py' packages.

## 3.6 Software Modules of the RealTime Part in the Arduino Leonardo

Due to the limitation in space and programmatic expressions of the Arduino Language (even though it is mostly C++ minus some possibilities) the structure of the Arduino Part is not as differentiated as the python part. The different functions are separated into different files which are represented as different Tabs in the Arduino IDE.

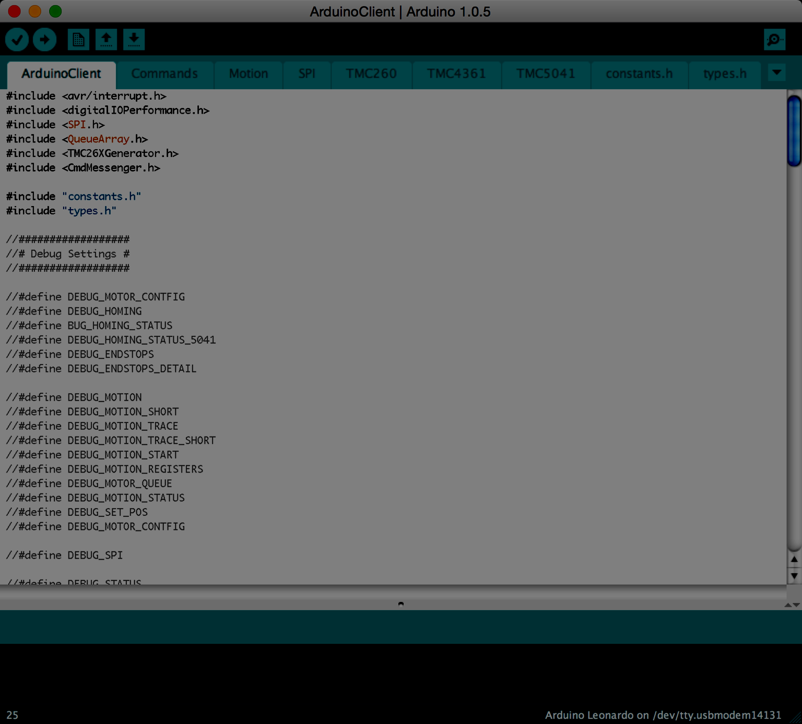
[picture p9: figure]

Figure 3 - Arduino Software

## 3.7 The Arduino Client itself

The module ArduinoClient contains the basic configuration of the Arduino Client the basic setup and loop routines to keep the program going and the include definitions to keep everything together. No special functions are implemented in this module.

## 3.8 The Commands Module

The Commands Module contains the interpretation and answering of the serial communication commands. It contains no real logic just the commands, it's numbers and parameters, the calls of the corresponding functions and the replies.

## 3.9 The Motion Module

The Motion module contain the main motion buffer (moveQueue) ,the information if currently a coordinated motion is executed (current_motion_state). If it is so it knows is a move is currently executed (move_executing) or the next move is prepare in the squirrel shadow registers (next_move_prepared). The move queue is a ring buffer which is filled from the serial interface and emptied by executing moves. If the next move is not prepared a move is read from the motion queue and written to the squirrel shadow registers. If an move is executed it tracks if all motors of the move (motor_status) reached it target (target_motor_status). If all motors reached the target a new start signal is send.

## 3.10 The SPI Module

The SPI Module contain the functions to read and set registers in the squirrel and TMC5041.

## 3.11 The TMC260 Module

The TMC260 Module contain some functions to write register values to the TMC260 connected to the squirrel motion controllers and basically initialize the TMC260 after booting. The configuration of the TMC260 itself is done with the TMC26XGenerator – which is derived from the TMC26XDriver.

## 3.12 The TMC4361 Module

The TMC4361 Module contain the setup code to correctly set the pins connected to the TMC4361 and and the functions to translate between the high level concepts and the TMC4361 registers.

## 3.13 The TMC5041 Module

The TMC5041 Module contain the setup code to initialize the TMC5041 after boot and the functions to translate between high level concepts and the TMC5041 register

## 3.14 The constants

The file constants.h contains all constant values and conversions used in other files. They are collected here to get them out of the way for other modules.

## 3.15 The types

The file types.h contain the typedef definitions to have them in one convenient place.

# 4 The Serial Communication Interface

As Serial Communication Interface CmdMessenger was choosen. It had the advantage of being human readable and writeable and implemted. An message or answer always consists of a number of comma separated values:
<command number>, <option 1>, <option 2> and so on. A command is ended by ';'
A example command could be 1,12.0,2,”test”; and be answered by 0,0;
Commands can contain options and parameters for integer values, floating point values and text. On Arduino integers and long are separated since on Arduino integers are only 16 bit wide.
Action Commands have positive command numbers. Answers have negative command numbers. 0 means OK.

## 4.1 Command 1: Set Motor Current

This command set the motor current for any axis. The parameters are
- The motor 1-5
- The current in mA
The current can only be set for the squirrel motors currently.
It is replied with OK or an error.

## 4.2 Command 2: Configure Encoder

This command is used to configure the encoder of an TMC4361 motor. It contains the following options:
- The motor 1-5
- -1 for disabling the encoder, 1 for enabling the encoder
- the steps per revolution for the motor
- the microsteps per step for the motor
- the increments per revolution for the encoder
- 1 if the encoder is differential, -1 if not
- 1 if the encoder direction is inverted
The last 5 options can be omitted if an encoder is disabled

## 4.3 Command 3: Configure Endstops

This command is used to configure the endstops of a motor. Either real endstops (home switches) or virtual endstops which are position based can be used.
It contains the following options for real endstops:
- The motor 1-5
- 1 for right and -1 for left endstop position
- 1
- -1 for an active low and 1 for an active high endstop For virtual endstops:
- The motor 1-5
- 1 for right and -1 for left endstop position
- 0
- The step position of the virtual endstop

## 4.4 Command 4: Invert Motor

This command inverst the direction of a motor movement. The parameters are
- The motor 1-5
- 1 for a non inverted motor, -1 for an inverted motor
If the second parameter is 0 the reply is OK and if the motor is inverted (e.g. 4,1,-1;)

## 4.5 Command 9: Initialize Motion

This command initializes all chips, resets the TMC4361 and flushes the movement queue.

## 4.6 Command 10: Add Move

The add move command adds a move of several motors to the motion queue. For each motor the following information is given:
- The motor 1-5
- The target of the movement as step position
- The movement type: 's' for a movement which stops at the given endpoint or 'w' for a movement which is continued after the current way point.
- The maximum speed of the movement in steps/s
- The maximum acceleration of the movement in steps/s^2
4.7 Command | 11: | Movement | information | and | finish

## movement

The movement command can be used to read out if the machine is currently executing a movment or to indicate the machine to finish a movement and empty the movement buffer.
It consist of these parameters:
- 0 for get movement information or a negative number to indicate to finish the movement

## 4.8 Command 12: Home Axis

This command can be used to drive a motor to the endstop to achieve it's actual physical zero position. The homing is achieved by first driving with the homing fast speed to the endstop, go back by the given retraction and slowly driving back into the endstop with the slow homing speed to achieve an very precise hit.
It consists of the following options:
- The motor 1-5
- the homing timeout
- the fast homing speed
- the precision homing speed
- the retraction after the motor first hits the endstop
- the acceleration of the homing movement
- for motors 1-3: The endstop position if the stop switch is on the far side of the motor range

## 4.9 Command 13: Set Position

The set position command can be used to set the internal step position of a motor. It consists of the following options:
- The motor 1-5
- The new position to set.
These positions are added to the move queue to move the motor to a position and set it there.

## 4.10Command 30: Read Position

This command can be used to read out the current motor position. It is not queued and answered directly. It contains the following options:
- The motor 1-5
The Answer consist of the following information:
- The current position

## 4.11 Command 31: Queue Status Readout

This command is answered with a number of queue status options:
- The current length of the execution queue
- The maximum length of the execution queue

## 4.12 Command 32: Read Status

This command reads the motor status. It contains the following options:
- The motor 1-5
This command is answered with some status information for the given motor. For TMC4361 motors:
- the status flags register
- the x actual register
- if the left endstop is active
- if the right endstop is active
- the the encoder position register For TMC5041 motors:
- the x actual position

# 5 Revision history

## 5.1 Document revision

Version | Date | Author | Description
0.1 | 2014-OKT | MN | Initial version
0.2 | 2014-NOV | LJ | Redesign
0.3 | 2015-FEB | SL | Update of command structure

Figure 5.1: Document revision

## 5.2 Software revision

Version | Date | Author | Description
T-Bone_V09 | 2013/2014 | Marcus Nowotny (interactive matters) | Initial version

Figure 5.2: Software revision

# 6 References

[agpl-3.0] | GNU Affero General Public License Additional information can be found on http://www.gnu.org/licenses/agpl-3.0.html

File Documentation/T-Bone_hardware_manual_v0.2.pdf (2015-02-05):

Hardware to control Desktop manufacturing plattforms | T-Bone

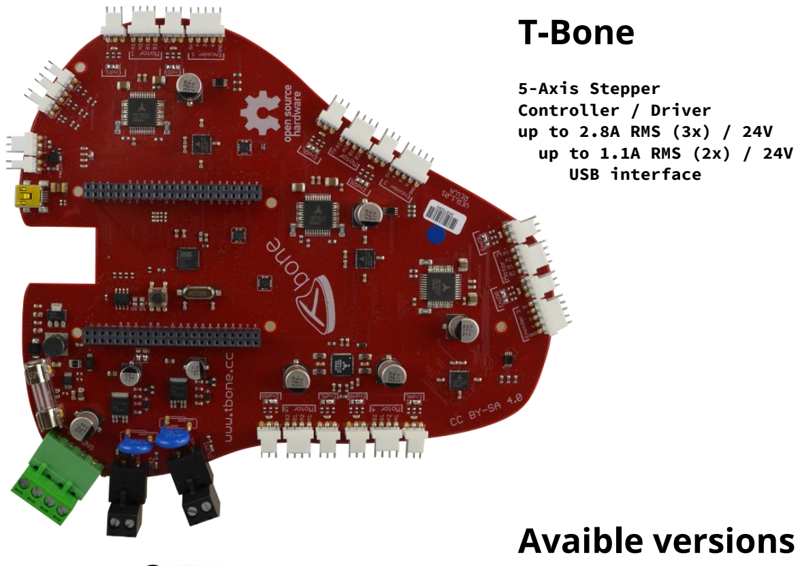
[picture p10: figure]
T-Bone; 5-Axis Stepper Controller / Driver up to 2.8A RMS (3x) / 24V up to 1.1A RMS (2x) / 24V USB interface; Avaible versions
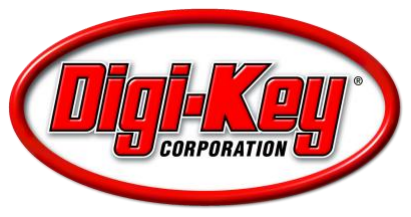
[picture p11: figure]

T-Bone Team
Hamburg, Germany

www.tbone.cc

V 0.2

# HARDWARE MANUAL

T-Bone Rare
T-Bone Medium
T-Bone Well-Done
T-Bone Deluxe

T-Bone BBQ (breakout board)

All used electronic components are available on:

T-Bone Hardware Manual (V0.1 / 2014-JUN-27) | 2

T-Bone Team

# Table of contents

# 1 License

The T-Bone Hardware documentation, with its schematics and board designs, is published under the Creative Commons Attribution-ShareAlike 4.0 International (CC BY-SA 4.0). [CCBYSA40]

The T-Bone software version is published under the agpl-v3.
Fur | further | information | please | visit
https://github.com/trinamic/t-bone

The T-Bone uses an Arduino Leonardo as a microprocessor. This is a derivate and is not connected to the Arduino Company. Any technical support needs to be provided directly to the T-Bone Team.

T-Bone Team 2014

# 2 Features

The T-Bone offers several features which are described in this section. The motors refer to a 3D-Printer hardware setup. So the notations may differ from the hardware labels since the T-Bone Hardware is useable for a wide range of desktop manufacturing platforms.

Stepper Drivers

The drivers for X, Y, and Extruder (Motor 1 – 3) are supporting a maximum motor current of 4A peak (2.8 RMS), 9…30V, and 1/256 microstep resolution. The drivers are connected with a bidirectional Serial Peripheral Interface (SPI). Therefore it is possible to control maximum motor current, step resolutions, and other features remotely.
The Z-axis (Motor 4 and 5) of the T-Bone are in fact two axis. They can be used to drive two motors for the Z-axis simultaneously or separate for e.g. an additional extruder. The maximum current is 1.5A peak (1.1A RMS), 1/256 microsteps, up to 24V.

Stepper Controller

Motor 1 - 3 are connected with dedicated motion controller chips. They are responsible for all real-time related activities, like calculation of the motor acceleration, maximum speed, and step count to target a certain position. They can operate with linear or s-shaped acceleration profiles (what’s the difference? You know it if you ever found your coffee-to-go on your shirt after the metro fitfully started to move.). S-Ramps reduce the jerk and make the movement smoother while accelerate and allow higher acceleration and thus faster movements. The Z-axes are using an integrated driver/controller chip doing the same job (beside the s-shaped ramp). All controllers are using the same clock rate, given by the Arduino™. The maximum step rate (microsteps per second) are depending on the clock rate and can be several MHz.

Arduino™-based Real-Time Controller

The stepper controllers are connected to an Atmel™ microcontroller, also with bidirectional SPI. Its main job is to send and receive data from the controllers and the BeagleBone™. Commands are buffered to decouple real-time operations of the T-Bone from the asynchronous UART interface to the BeagleBone™. Optionally the Atmel™ can also control the power switches for the extruder, heat bed, and fan. Also the thermistors are connected to both sides. (In case of controlling a 3D-Printer)
The Atmel microcontroller is running with the Arduino™ firmware. Therefore it’s easy to modify the communication protocol for improvement or special requirements.

Comparison to other solutions

Most other solutions are using stepper drivers with unidirectional step/direction interface. These are two wires controlling the step rate of the motor and the rotation direction. Microstep resolution and maximum motor current are mostly fixed. Some solutions offer the possibility to set the current by an analog input pin.
The generation of the step rate, acceleration, maximum speed and positioning are usually done by the same Arduino™ which is also responsible for host communication, G-Code interpretation, and path planning. Therefore the maximum step rate and complexity of ramp generation is quite limited. Most solutions offer step rates of 10 – 20 kHz and are restricted to linear acceleration ramps.
| T-Bone | Others
| X, Y, Ext. | Z | All
Max Current | 4A | 1.5A | 2A
RMS Current | 2.8A | 1.1A | 1.4A
Microstepping | 1/256 | 1/256 | 1/16
Step Rate | 16 MHz | 16 MHz | 10 – 20 kHz
Set Step Resolution | Digital | Digital | fixed
Set Current | digital | Digital | fixed/analog
Acceleration | linear, s-shaped | Linear | Linear

Table 2.1 - Comparision with other products

Special features of the driver

The stepper driver chips of the T-Bone have some unique features. The most notable is the stallGuard2™ function. By measuring the electronic impulses coming back from the motor, the driver can “see” the current mechanical load of the axis. If the motor is blocked by a mechanical end stop, this is recognized and can be feeded back to the control electronics. It is also possible to adjust the motor current to the load level to increase the energy efficiency. This technology is calles coolStep™.
To enable stallGuard2™ the control software has to be slightly modified. The user also needs to set some additional parameters to adjust the sensing electronics to the particular characteristics of the used motor.

Applications examples for the T-Bone electronic
- 3D-Printers
- Milling machines
- Laser cutters
- Many many more

Electrical data
- Supply voltage: +12V … +24V DC nominal
- Motor current: 4A (2.8A RMS) X-, Y- , Extruder-Axis, 1.5A (1.1A RMS) Z-Axis

Integrated motion controller
- Motion profile calculation in real-time (TMC4361 and TMC5041 motion controller)
- On the fly alteration of motor parameters (e.g. position, velocity, acceleration)

Integrated bipolar stepper motor driver
- Up to 256 microsteps per full step
- High-efficient operation, low power dissipation (MOSFETs with low RDS(ON))
- Dynamic current control
- Integrated protection
- stallGuard2™ feature for stall detection
- Automatic load dependent motor current adaptation for reduced power consumption and heat dissipation (coolStep™)

Interfaces
- USB full speed (12Mbit/s) device interface to communicate with the ATmega32u4 (“Arduino Leonardo”)

Software
- Arduino firmware for 3D-Printer support
- Beagle Bone python scripts for easily setting up the hardware and communicate with the ATmega32u4 over serial communication (UART0 & UART2)
- Beagle Bone web interface to control 3D-Printer via web interface and get live status

# 3 Order codes

The T-Bone is available in different versions. In the following table the versions are described and the related order codes are listed.

Version | Description
T-Bone Rare | Bare T-Bone board without components
T-Bone Medium | T-Bone board with SMD parts assembled. THT parts enclosed but unassembled
T-Bone Well-Done | Fully assembled T-Bone cape, ready to run. (Beagle Bone Black not included)
T-Bone Deluxe | Fully assembled T-Bone with preconfigured Beagle Bone Black Rev. C
BBQ Board | Breakout board for TRINAMIC ICs with several footprints

Table 3.1 : Available products

# 4 Mechanical and electrical interfacing

The T-Bone consists of a board which is designed to fit on top of the Beagle Bone Black single board computer.

## 4.1 Size of electronics

The T-Bone board with the controller / driver electronics has an overall size of 158.5mm x 185.8mm and four mounting holes in order to fit on the top of the Beagle Bone Black. The mounting holes have been designed for M3 screws (size of mounting holes: 3.2mm diameter each). There are two additional mounting holes to be able to screw the board on any surface.

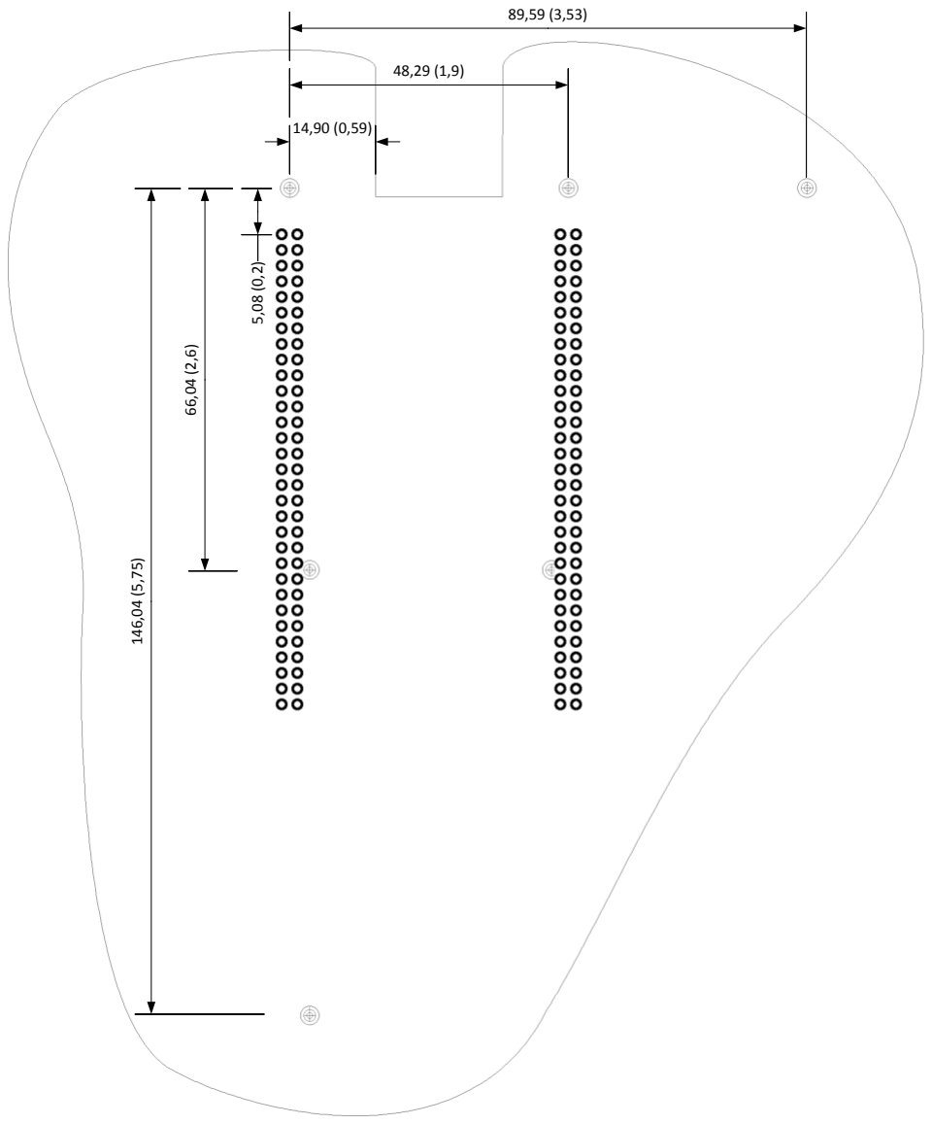
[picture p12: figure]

Picture 4.1 - Board dimensions and position of mounting holes

## 4.2 Connectors

The T-Bone offers four connectors, a 6pin power and communication connector, an 8pin multi-purpose I/O connector, a 4pin motor connector and a mini-USB connector.

Overview of connector and mating connector types:
Label | Connector type
Power supply connector | Phoenix-Contact TERM BLOCK HDR 4POS R/A 5.08MM
High power outputs | Molex TERM BLOCK HDR 2POS R/A 5.08MM
Motor Connector | TE-Connectivity CONN HEADER RTANG 4POS .100 TIN
Endstops | TE-Connectivity CONN HEADER RTANG 3POS .100 TIN
Encoders | TE-Connectivity CONN HEADER RTANG 5POS .100 TIN
Temperature Inputs | TE-Connectivity CONN HEADER RTANG 2POS .100 TIN
Fan Output | TE-Connectivity CONN HEADER RTANG 2POS .100 TIN
1-Wire | TE-Connectivity CONN HEADER RTANG 2POS .100 TIN
USB connector | CONN USB MINI B

Table 4.2: Connectors and mating connectors, contacts and applicable wire

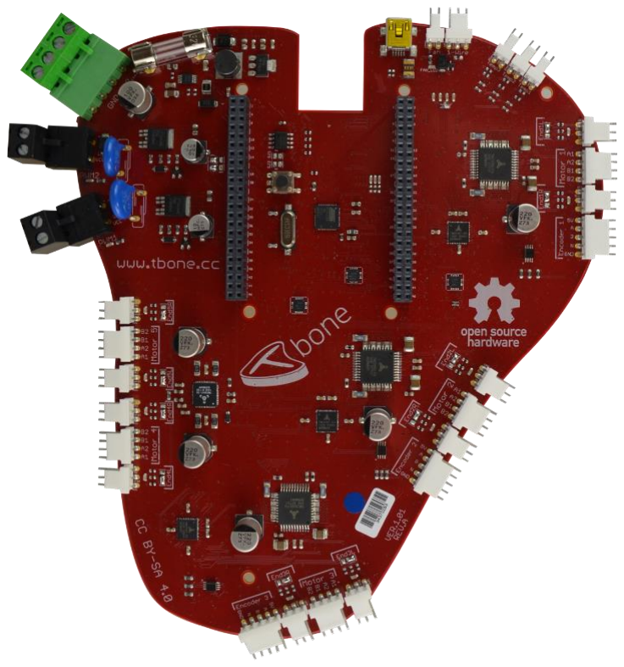
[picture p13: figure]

Figure 4.3: T-Bone connectors

## 4.2.1 Power Connector

A 4 pin with fuse between input and 24V VDD supply rail.
1 2 3 4 | Pin | Label | Direction | Description
| 1 | VDD | Power (Supply) | VDD (+12V…+24V)
| 2 | VDD | Power (Supply) | VDD (+12V…+24V)
| 3 | GND | Power (GND) | GND
| 4 | GND | Power (GND) | GND

Table 4.3: Power connector

# There is no reverse polarity protection!

## 4.2.2 High power output connectors

A 2 pin connector is available to connect high power devices such as heating cartridges or heating for 3D-

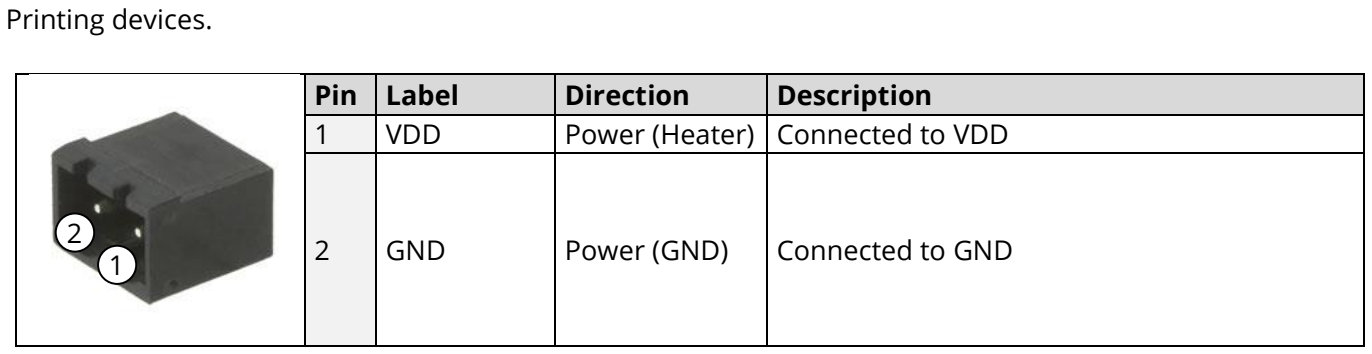
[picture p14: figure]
Printing devices.; Pin; Label; Direction; Description; VDD; Power (Heater); Connected to VDD; GND; Power (GND); Connected to GND

Table 4.4: High power output connectors

## 4.2.3 Motor connector

As motor connector a 4pin MOLEX 2,54mm pitch single row connector is available. The motor connector is used for connecting the four motor wires of the two motor coils of the bipolar stepper motor to the electronics.

B2 B1 A2 A1 | Pin | Label | Direction | Description
| 1 | B2 | Output | Pin 2 of motor coil B
| 2 | B1 | Output | Pin 1 of motor coil B
| 3 | A2 | Output | Pin 2 of motor coil A
| 4 | A1 | Output | Pin 1 of motor coil A

Table 4.5: Motor connector

Example for connecting a TRINAMIC QS4218 stepper motor:

A | M black

green

B blue
red
T-Bone | QS4218 motor
Motor connector pin | Cable colour | Coil | Description
1 | Black | A | Motor coil A pin 1
2 | Green | A- | Motor coil A pin 2
3 | Blue | B- | Motor coil B pin 2
4 | Red | B | Motor coil B pin 1

## 4.3 Mini-USB connector

A 5pin mini-USB connector is available on-board for serial communication with the derivated Arduino Leonardo (ATmega 32u4)

5 1 | Pin | Label | Direction | Description
| 1 | VBUS | Power | +5V supply from host
| 2 | D- | Bidirectional | USB Data –
| 3 | D+ | Bidirectional | USB Data +
| 4 | ID | Power (GND) | Connected to signal and system ground
| 5 | GND | Power (GND) | Connected to signal and system ground

Table 4.6: Connector for USB

## 4.4 Power supply

For proper operation care has to be taken in regard to power supply concept and design.

# There is no reverse polarity protection!

## 4.5 Communication

## 4.5.1 USB

For remote control and communication with a host system the T-Bone provides a USB 2.0 full-speed (12Mbit/s) interface (mini-USB connector). As soon as a USB-Host is connected the T-Bone is available as a common Arduino Leonardo in the Arduino IDE software.

The T-Bone supports USB self powered operation (when an external power is supplied via the power supply connector) and USB bus powered operation, also (no external power supply via power supply connector). During USB bus powered operation, only the communication to the Arduino Leonardo is available. Motor movements will not be possible. This mode has been implemented in order to enable configuration / parameter setting / read-out, firmware updates etc. by just connecting a USB cable between the T-Bone and a host PC. No additional cabling / external devices as e.g. power supply etc. are required in that case.

## 4.6 Inputs and outputs

## 4.6.1 High power outputs (2x – PWM controller)

The two pin connector of the T-Bone controls the heating bed and the hot end in the application of a 3D-Printer. The

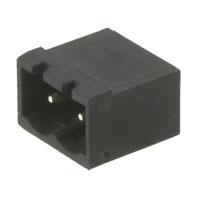
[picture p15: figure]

Figure 4.7: The two high power outputs

## 4.6.2 Motor connectors (5x)

The four pin connectors of the T-Bone are used to connect bipolar stepper motors.

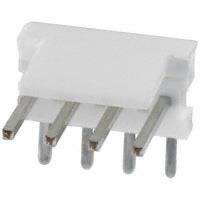
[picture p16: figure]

Figure 4.8: The five motor connectors

## 4.6.3 Endstop connectors

The ten endstop connectors of the T-Bone offer the possibility to limit the maximum travel range of the separate axis. For a 3D-Printer for example, there are two inputs for limiting switches for each axis. It is possible to connect all kind of end stop types since there is a +3V3 voltage, a GND and a signal conection.

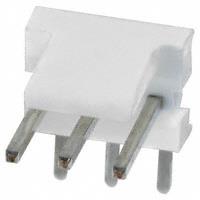
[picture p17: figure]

Figure 4.9: Endstop connectors for the motion controller

## 4.6.4 Low power Output (PWM controlled)

The T-Bone provides one output for low currencies. In case of a 3D-Printer this output would be used to connect a fan. This offers the possibility to regulate the temperature in combination with the high power outputs with a PID-controller algorithm.

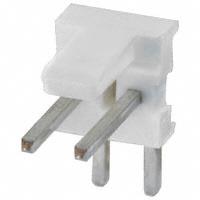
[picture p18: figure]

4.2 - Low power connector

## 4.6.5 One-Wire bus connector

To connect a One-Wire device, this connector is reserved. This could be a temperature sensor for example.

4.3 - One-Wire connector

## 4.6.6 Encoder inputs

Since the used motion controllers on this board provide the possibility to use a close-loop operation mode, there are 3 inputs for encoders. These

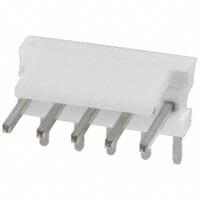
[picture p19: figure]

Figure 4.9: Encoder connectors

# 5 Functional description

The T-Bone is using a smart and proven concept for improvement and simplification at the same time: division of work. Dedicated motion control units are executing low-level, but time-critical functions. The BeagleBone can concentrate on complex tasks and user interfacing. Both parts are connected by an Arduino-compatible microcontroller, decoupling high-level and real-time programming.

The connection between the two boards is realized by a asynchronous UART interface. It’s easy accessible in software, offers high data rates, and decouples the task-driven BeagleBone and the real-time operation of the T-bone.

The T-Bone contains the following main components:

- ATmega™ 32u4 microcontroller programmed as Arduino Leonardo running with 16MHz
- 256Kbytes EEPROM for storing configuration parameters for the Beagle Bone Black via the I²C bus [BBB_SRM]
- TMC4361 [TMC4361] motion controller
- TMC2660 [TMC2660] advanced stepper motor driver IC with stallGuard2™ and coolStep™
- TMC5041 [TMC5041] stepper controller-driver IC

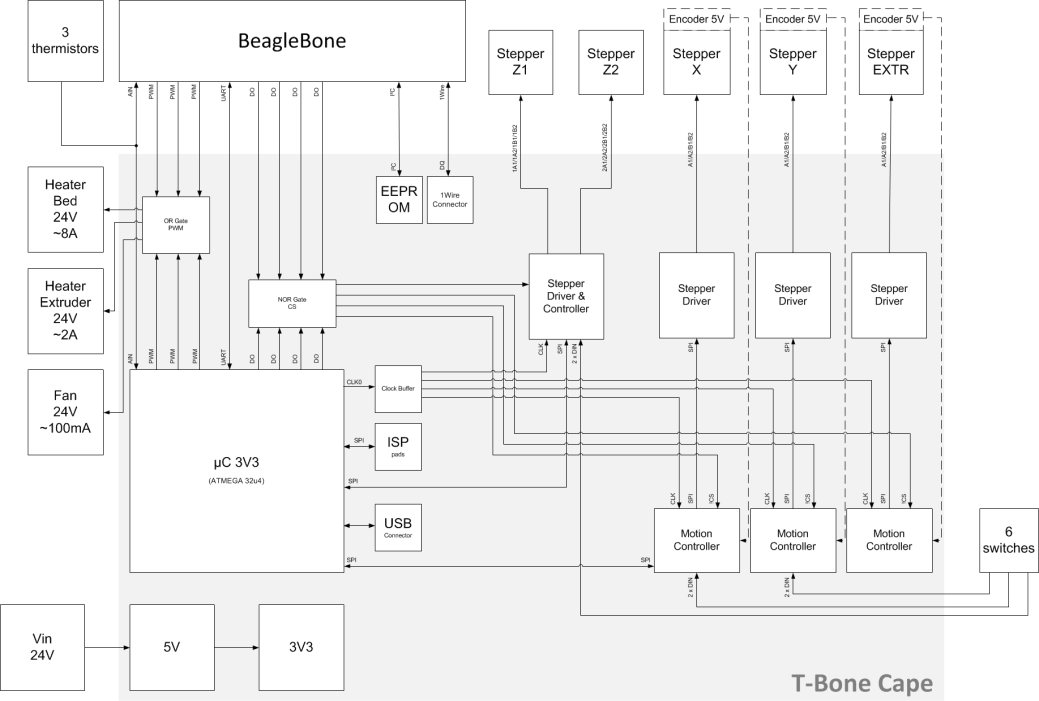
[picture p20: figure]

Figure 5.1: T-Bone block diagram

# 6 Startup operation instructions

This section will explain the steps to start up the T-Bone. In general it is possible to control the T-Bone with all devices which can establish a communication via UART e.g. Computer with respective interface, a Beagle Bone, a Raspberry Pi, an Arduino, etc.

There are many ways to use the T-Bone board. First it is described how the T-Bone is set into operation with a PC and a USB TTL Serial Cable. (Part Number: TTL-232-R-3V3)

First of all connect the motors you want to drive with the T-Bone. Afterwards connect a power supply in a range of 12V to 24V. Where the power supply voltage is connected to PIN 1 and 2 and GND is connected to PIN 3 and 4 (Subchapter 4.2.1). In this case an old Hewlett Packard Power supply is used. It provides a voltage of 18V.

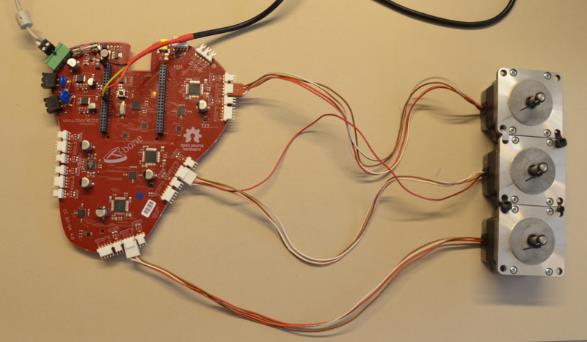
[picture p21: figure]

Figure 2 - T-Bone connected with motors, power supply and TTL-232R-3V3

As on Figure 5.1 seen a TTL-232R-3V3 FTDI to Serial converter is connected. With this device you are able to send and receive commands. Just connect the GND pin of the converter with the pin 1, 2, 43, 44, 45 or 46 of P9. P9 is on the left of the T-Bone with the orientation seen on Figure 5.1. Connect the TXD cable of the converter with P9 pin 24 and the RXD cable with P9 pin 26.

Now you are good to send the first instruction via a terminal program like HTerm. In this case the version 0.8.1beta was used. On the Figure 3 below you can see the program set up, to communicate with the T-Bone. The received command -128,0,40; is send every second by the Arduino Leonardo and represents a heartbeat.

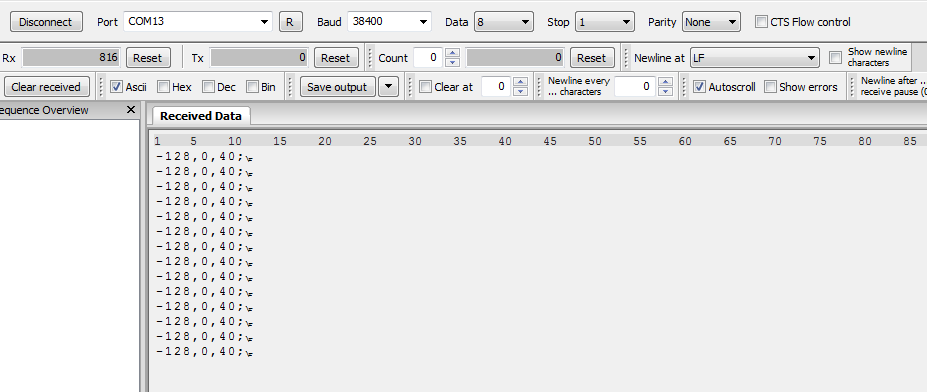
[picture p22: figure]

Figure 3 - HTerm set up receiving the heartbed of the T-Bone

## 6.1 Command set

Set Motor Current
1,<motor 1..5>,<current [mA]>;

Configure Encoder
2,<motor 1..3>,<enable=1/disable=-1>,<fs/rev motor>,<ustepping>,<increments encoder>,<1=differential/-1=single ended>,<inverted>;

Configure Endstops
Virtual Endstop: 3,<motor 1..5>,<1=right/-1=left>,0,<virtual endstop position>; Real Endstop: 3,<motor 1..5>,<1=right/-1=left>,1,<-1=active low/1=active high>;

Invert Motor
4,<motor 1..5>,<1=non inverted/-1=inverted>

Initialize Motion
9;

Add Move
10,<motor 1..5>,<target position>,<115=stop at target/119=continue motion>,<Vmax>,<Amax>,0; ^^^^^^^^^^^^^^^^^^^^^^^^^^^^^^^^^^^^^^^^^^^^^^^^^^^^^^^^^^^^^^^^^^^^^^^^^^^^^^^^^^^^^^^^ Can be repeated, e.g.:
10,1,1000,115,100000,500000,0,2,2000,115,200000,1000000,0,3,1500,115,150000,750000,0;

Movement information
11,0;

Finish Movement
run from queue: 11,1;
empty queue: 11,-1;

Home axis
12,<motor 1..5>,<timeout>,<fast speed>,<slow speed>,<retract>,<aMax>...

Set Position
13,<motor 1..5>,<new position>;

Read Position
30,<motor 1..5>;

Queue status readout
31;

Read motor status
32,<motor 1..5>;
Returns: 32,<status register>,<Xactual>,<left endstop: 1=active/-1=inactive>,<right endstop: 1=active/-1=inactive>,<encoder position>;

## 6.2 Example command instruction set

Run motor 3 with 750mA (RMS):
Position | Velocity | Acceleration
102400 | 204800 | 819200
0 | 204800 | 819200
102400 | 204800 | 819200
0 | 204800 | 819200

Table 2 - Target parameters for example instruction set

9;
//Initialization

1,3,750;
//Set motor current to 750mA of motor axis 3

10,3,102400,115,204800,819200,0;
//Add first movement into motion queue (row 1 of table 3)

10,3,0,115,204800,819200,0;
//Add second movement into motion queue (row 2 of table 3)

10,3,102400,115,204800,819200,0;
//Add third movement into motion queue (row 3 of table 3)

10,3,0,115,204800,819200,0;
//Add fourth movement into motion queue (row 4 of table 3)

11,1;
//Run

11,-1;
//Empty queue

# 7 Operational ratings

The operational ratings show the intended or the characteristic ranges and should be used as design values.

In no case shall the maximum values be exceeded!

Symbol | Parameter | Min | Typ | Max | Unit
VDD | Power supply voltage for operation | 12 | 24 | 24 | V

TMC2660

ICOIL_peak | Motor coil current for sine wave peak (chopper regulated, adjustable via software) | 0 | | 2.8 | A
ICOIL_RMS | Continuous motor current (RMS) | 0 | | 2.0 | A

TMC5041

ICOIL_peak | Motor coil current for sine wave peak (chopper regulated, adjustable via software) | 0 | | 2.8 | A
ICOIL_RMS | Continuous motor current (RMS) | 0 | | 2.0 | A

Table 7.1: General operational ratings of module

# 8 Revision history

## 8.1 Document revision

Version | Date | Author | Description
0.1 | 2014-JUN | LJ | Initial version
0.2 | 2015-FEB | LJ

Figure 8.1: Document revision

## 8.2 Hardware revision

Version | Date | Description
T-Bone_V09 | 2014-FEB | Prototype
T-Bone_V100 | 2014-MAR
T-Bone_V101 | 2014-JUN

Figure 8.2: Hardware revision

# 9 References

[TBONE] | T-Bone Team homepage Support system can be found on http://www.tbone.cc/
[TMC4361] | TMC4361 datasheet Additional information can be found on http://www.trinamic.com
[TMC2660] | TMC2660 datasheet Additional information can be found on http://www.trinamic.com
[TMC5041] | TMC5041 datasheet Additional information can be found on http://www.trinamic.com
[BBB_SRM] | Beagle Bone Black system reference manual Additional information can be found on http://www.beagleboard.com/
[CCBYSA40] | Creative Commons Attribution-ShareAlike 4.0 International Additional information can be found on https://creativecommons.org/licenses/by-sa/4.0/

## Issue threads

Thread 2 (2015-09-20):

Can somone tell me how and which software i update now!?

mo22de, 2015-09-20:
I got the T-bone with BBB and tried the way the "Software Update instructions.pdf says.

After i needed to input a passphrase i dont get with the board i had a closer look, there was my first issue.

Well i created a new key, but agin failed. So i figured out that the repo that was cloned doesnt exist anymore, it was hosted by git@github.com:interactive-matter/trinamic3d.git so the git pull wont work for me

I dont try to simply change the upstream, instead i backup the folder and tried to clone a new one, but which one is the new one now? I mean you have :https://github.com/trinamic/T-Bone
But when i look in the Wiki it says i should clone this:
git clone https://github.com/maggo1404/T-Bone.git

However i just cloned the maggo one for now and will see how far i will come.

My motors get super hot after some minutes that you can burn your skin, is that normal?

So, can someone tell me how to set it up right?
Or giv e a resource or somthing?

mo22de, 2015-09-21:
OK, here's some progress of geting aware of what happend.

-This Repo was once hosted via interactive-matter/trinamic3d

-The deluxe Version comes with this repo installed on a Angstrom Linux on BBB Rev B not C as told at indiegogo, just to mention.

-The Software Update instructions.pdf at T-Bone/Documentation/ says to update Software via git pull, which cant work caused of two problems:

  - 1st the ssh rsa eyphrase is unknown
  - 2nd the repo doesn't exist anymore

-This leads me to the Wiki of this repo which says to install first -debian and then clone another repo fork at https://github.com/maggo1404/T-Bone.git

! And now nothing works anymore.

########################################################################

I'm willing to do a proper documentation when i got it right.
But may somone allready can give some support

By the way after i opened a ticket at the trinamic support platform, my account didnt worked after the last email to me.
My suport ticked was opened because i was and am still missing a T-Bone BBQ as i ordered 2 at indiegogo and just get one as i described.

Again I supportetd the project by ordering some perks
1x deluxe
1x medium
1x rare
2x BBQ

an 1x BBQ still missing.

So maybe somone can contact me via mo22de@gmail.com or help me here to get this board running.
Meanwhile i will get through the code and try different things to get it running myself, but any help would be appreciated.

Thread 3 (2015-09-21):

Attention TTL example code from documentation grilled my motor 3 driver chip to magic smoke

mo22de, 2015-09-21:
After going through the hardware documentation i found chapter 6 "Startup operation instructions"

As it says it helps start up th T-Bone.

Using the same software and firing the example commands from chapter 6.2 the motor starts doing some moves.
But after some more moves the driver chip for motor 3 just explodes while the motor gets super hot. The motor is a QSH 4218-51-10-049 as the dalso examples TRINAMIC QS4218 stepper motor i got those and also double checked the wiring.

So any idea why the driver explodes?

Im lucky to have another t-bone board but im now affraid to wire it up :-P
As the rest of the board seems ok, i will buy a new TMC2660 and replace the broken one, but I dont know why that happens. Also it was interesting to see that sometimes it moves just once, but than again 4 times as the example shows.

Sometimes just the fan1 led comes up, and even more confusing, sometimes motor 1 spins too??

jcoffland, 2016-04-26:
@mo22de  We are also having problems with the TMC2660 driver chips blowing up.  Have you had any more problems like this?  Found any solutions?

trinamic, 2016-04-28:
Dear Joseph,

Thank you very much for your message.

To improve our service and make it much efficient we create a ticket system for technical questions.
Please make a short log in and create a ticket. Our R&D will answer usually within 24h.
http://www.trinamic.com/support/support-request

If you have questions please do not hesitate to contact us.

Best regards,

Your TRINAMIC Team
--------------------------------------------
TRINAMIC Motion Control GmbH & Co KG
Waterloohain 5 • D-22769 Hamburg • Germany
fon:     +49-40-514806-0
fax:     +49-40-514806-60
follow us on twitter<https://twitter.com/Trinamic_MC>
--------------------------------------------
Handelsregister / Court of Registration: Hamburg, HRA 100972
Managing Directors / Geschäftsführer: Bernhard Dwersteg, Dr. Lars Larsson, Michael Randt

The information contained in this e-mail is confidential or may otherwise be legally privileged. It is intended for the named recipient only. If you have received it in error, please notify us immediately by reply or by calling the telephone number above and delete this message and all its attachments. Please note that any unauthorised review, copying, disclosing or otherwise making use of the information is strictly prohibited. Thank you!

Die Information in dieser E-Mail einschließlich ihrer Anhänge ist vertraulich und ist daher allein für den Gebrauch durch den vorgesehenen Empfänger bestimmt. Dritten ist das Lesen, Verteilen oder Weiterleiten dieser E-Mail sowie jedwedes Vertrauen auf deren Inhalt untersagt. Wir bitten sie daher eine fehlgeleitete E-Mail unverzüglich vollständig zu löschen und uns eine Nachricht zukommen zu lassen. Danke!

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

MisterScott, 2017-03-29:
I would appreciate knowing whether and how this issue was resolved.  Thanks in advance!

jcoffland, 2017-03-29:
We struggled for months trying to get the ``tmc2660`` not to smoke under load or hostile conditions such as sudden power removal.  Eventually we gave up and moved on to a different design.  The features of the ``tmc2660`` are interesting but in the end we just couldn't make it work reliably even after several iterations of our board and listening to suggestions from Trinamics.  They did work well for small loads.  <1A range.

mo22de, 2017-04-26:
I also froze to get these things running, a little disappointing while supporting the campaign buying 2 full assembled, a bare PCB t-bone and some add-ons. I never got the board running and there is not much resource to learn from.
At trinamics i tried a fiew times to get support, but after an initial support request i got blokced somehow from the support forum and cant get logged in to that platform since. Im also still waiting for an answere of a non-delivered part i ordered and payed for via indigogo campaign. So i dont see to get involved in any more trinamic chips for my designs even if those chips should have advantages compared to others, if i cant relay on shipping or basic support im out.

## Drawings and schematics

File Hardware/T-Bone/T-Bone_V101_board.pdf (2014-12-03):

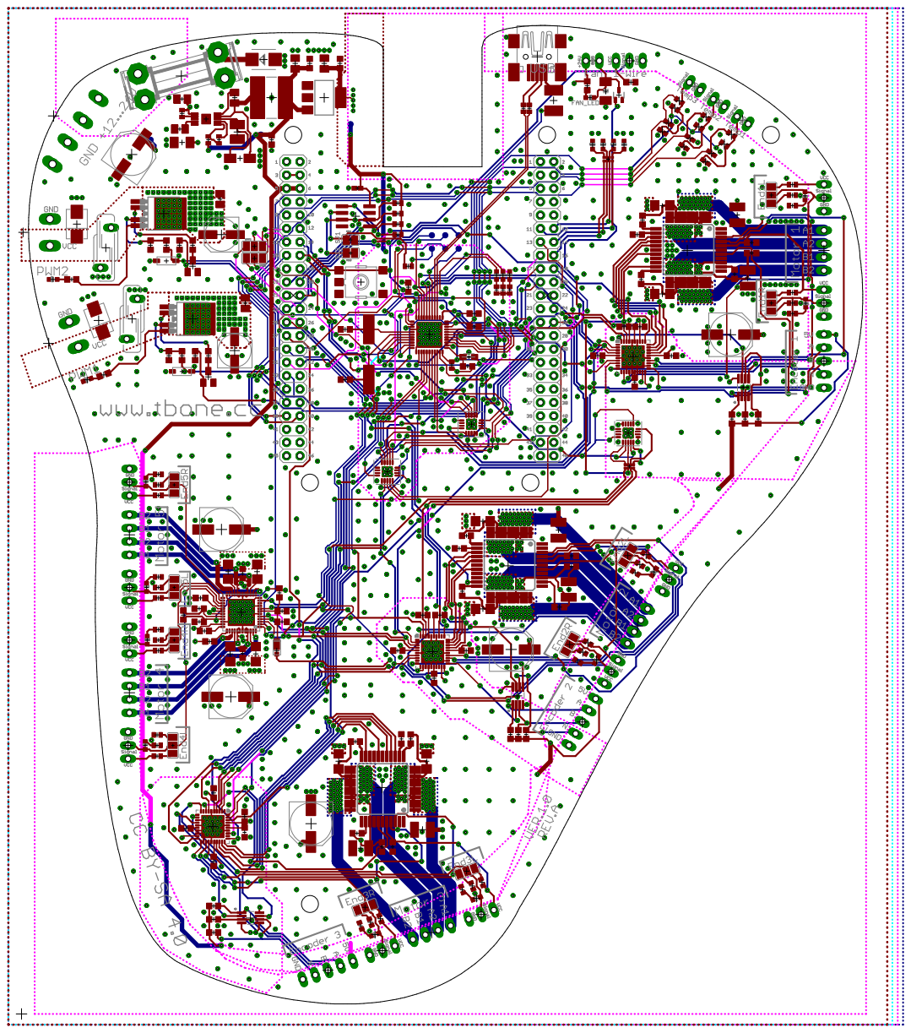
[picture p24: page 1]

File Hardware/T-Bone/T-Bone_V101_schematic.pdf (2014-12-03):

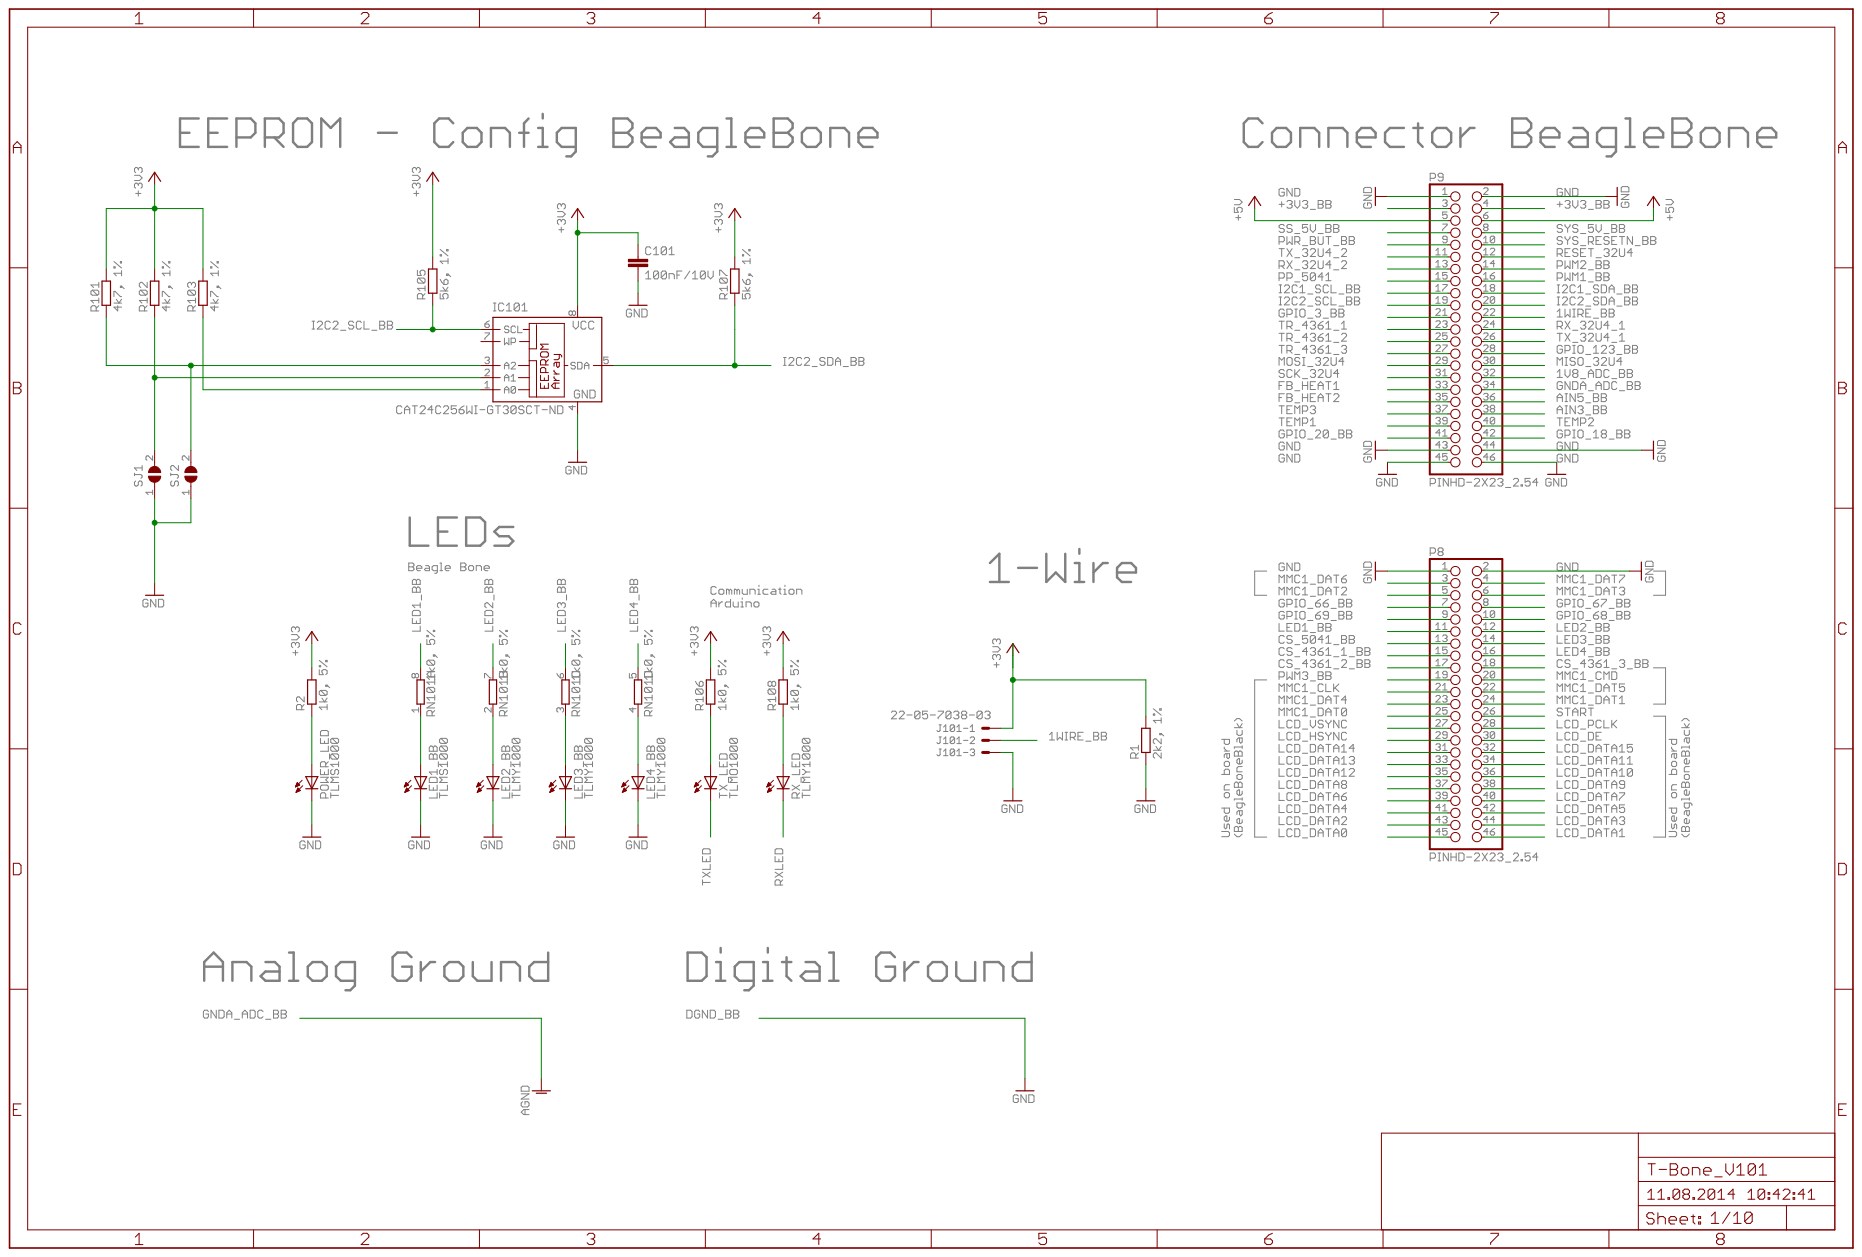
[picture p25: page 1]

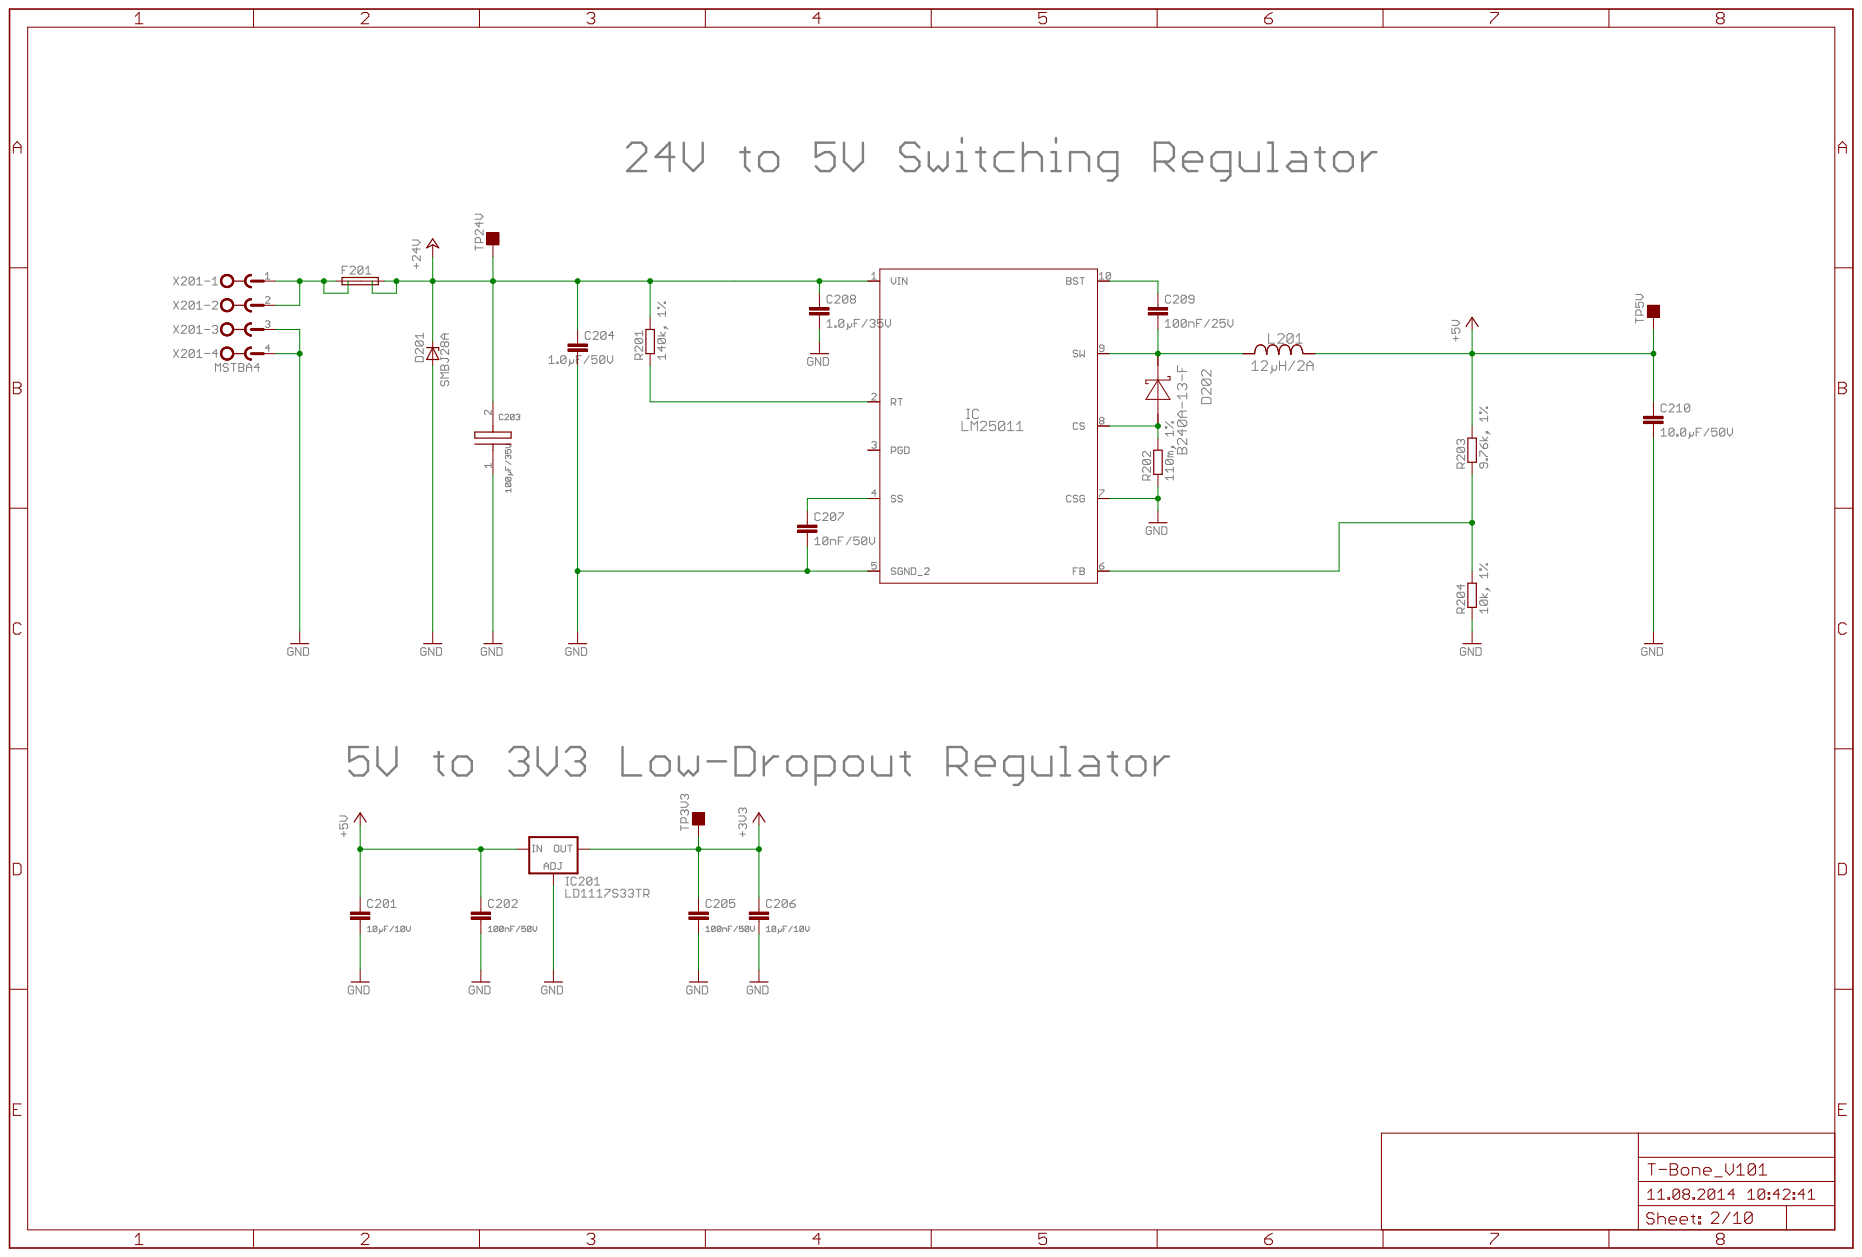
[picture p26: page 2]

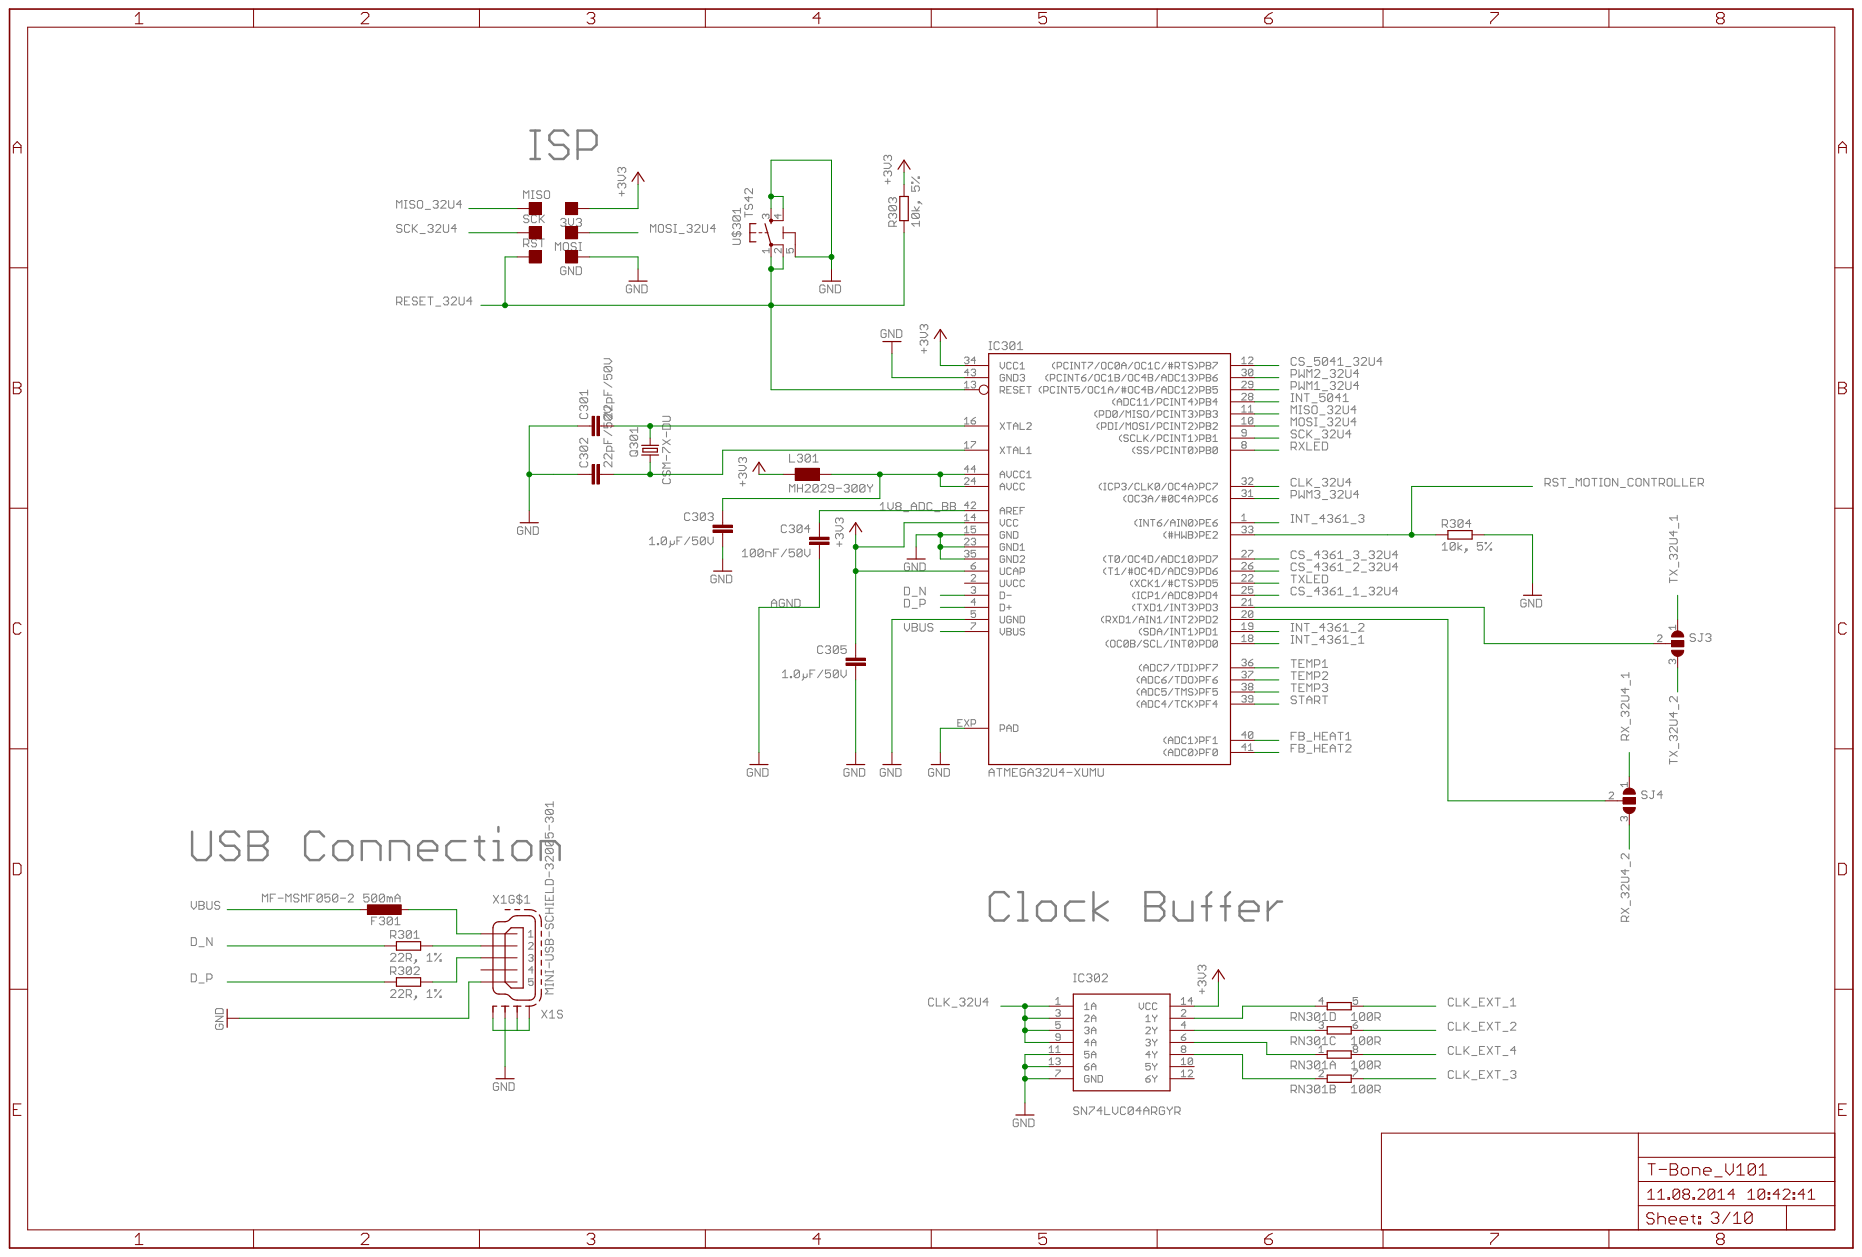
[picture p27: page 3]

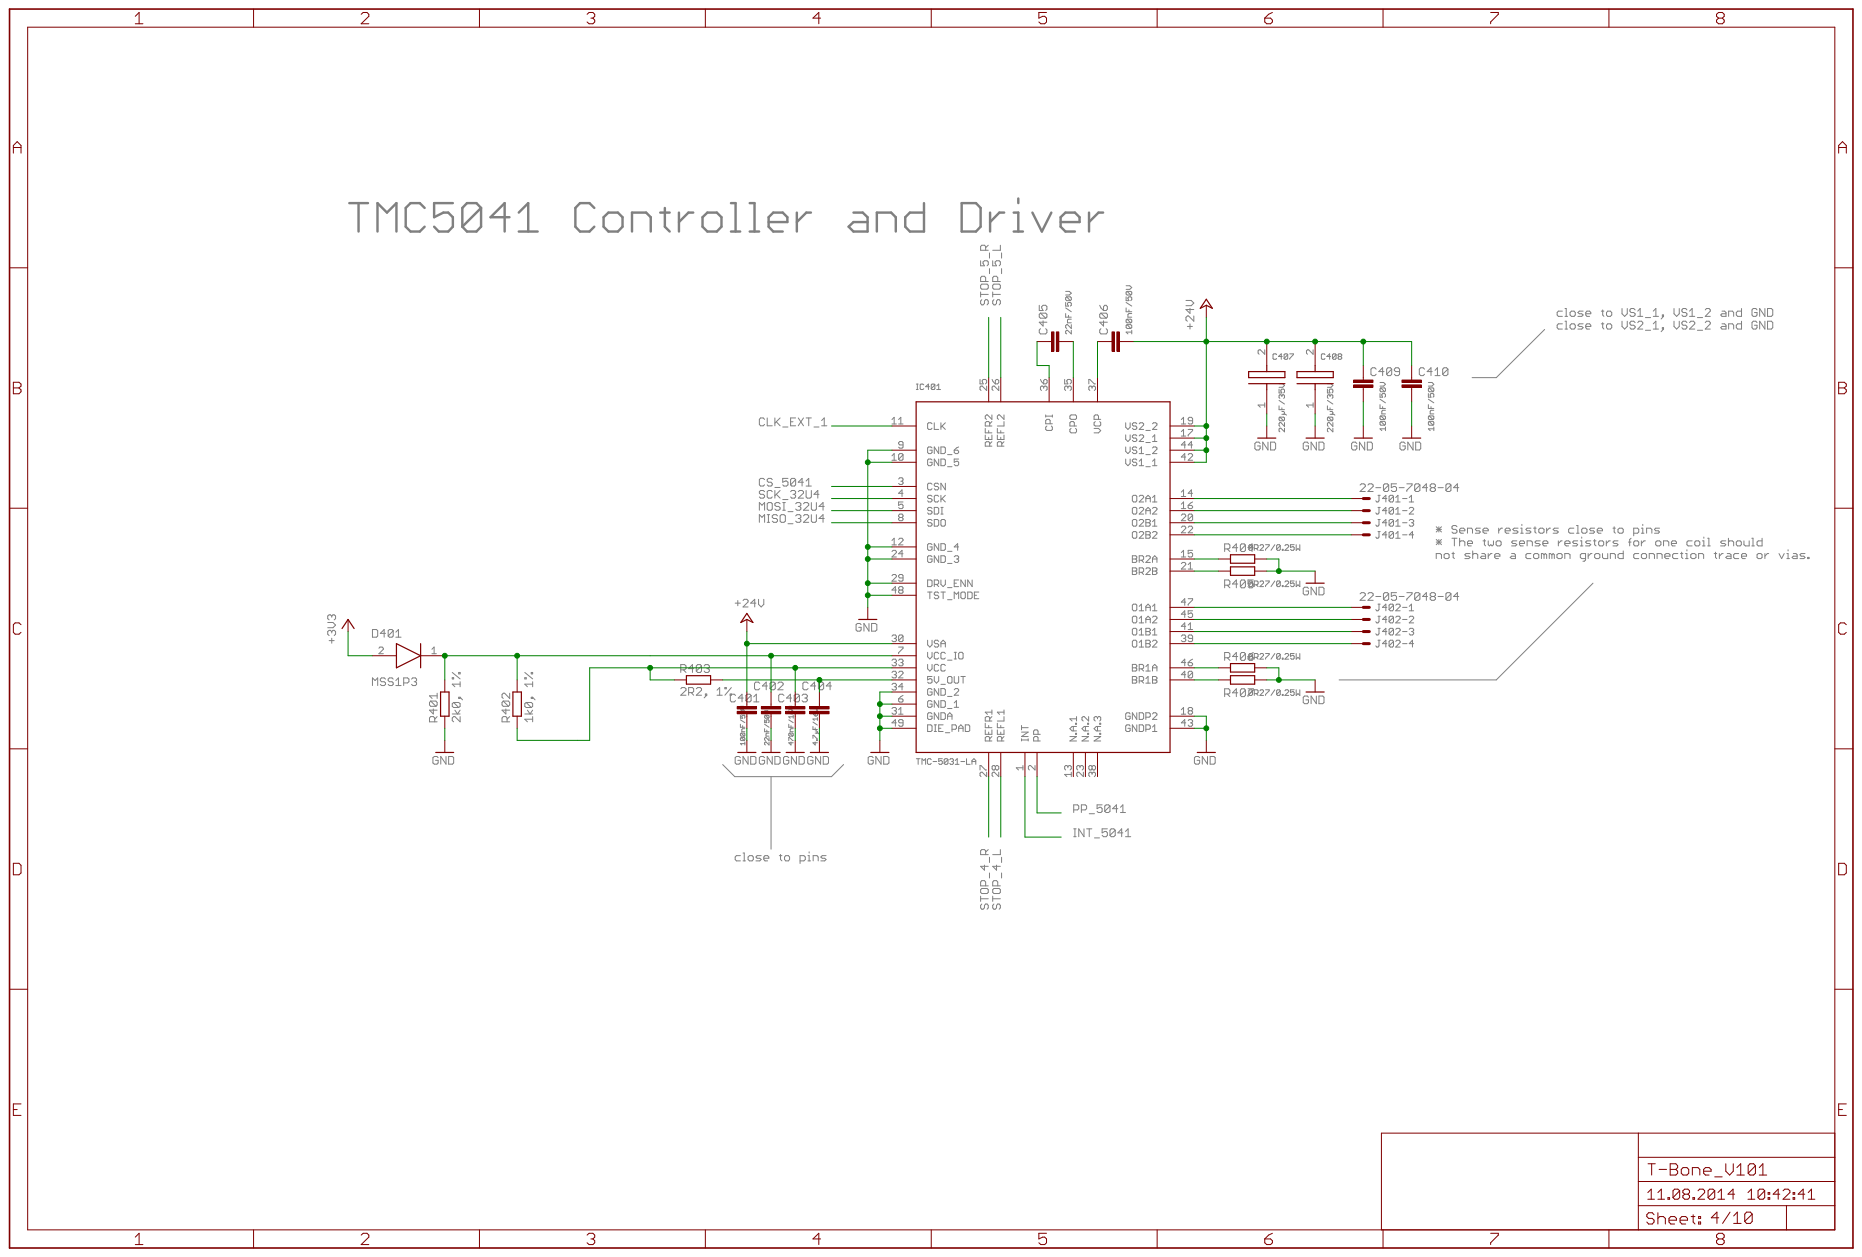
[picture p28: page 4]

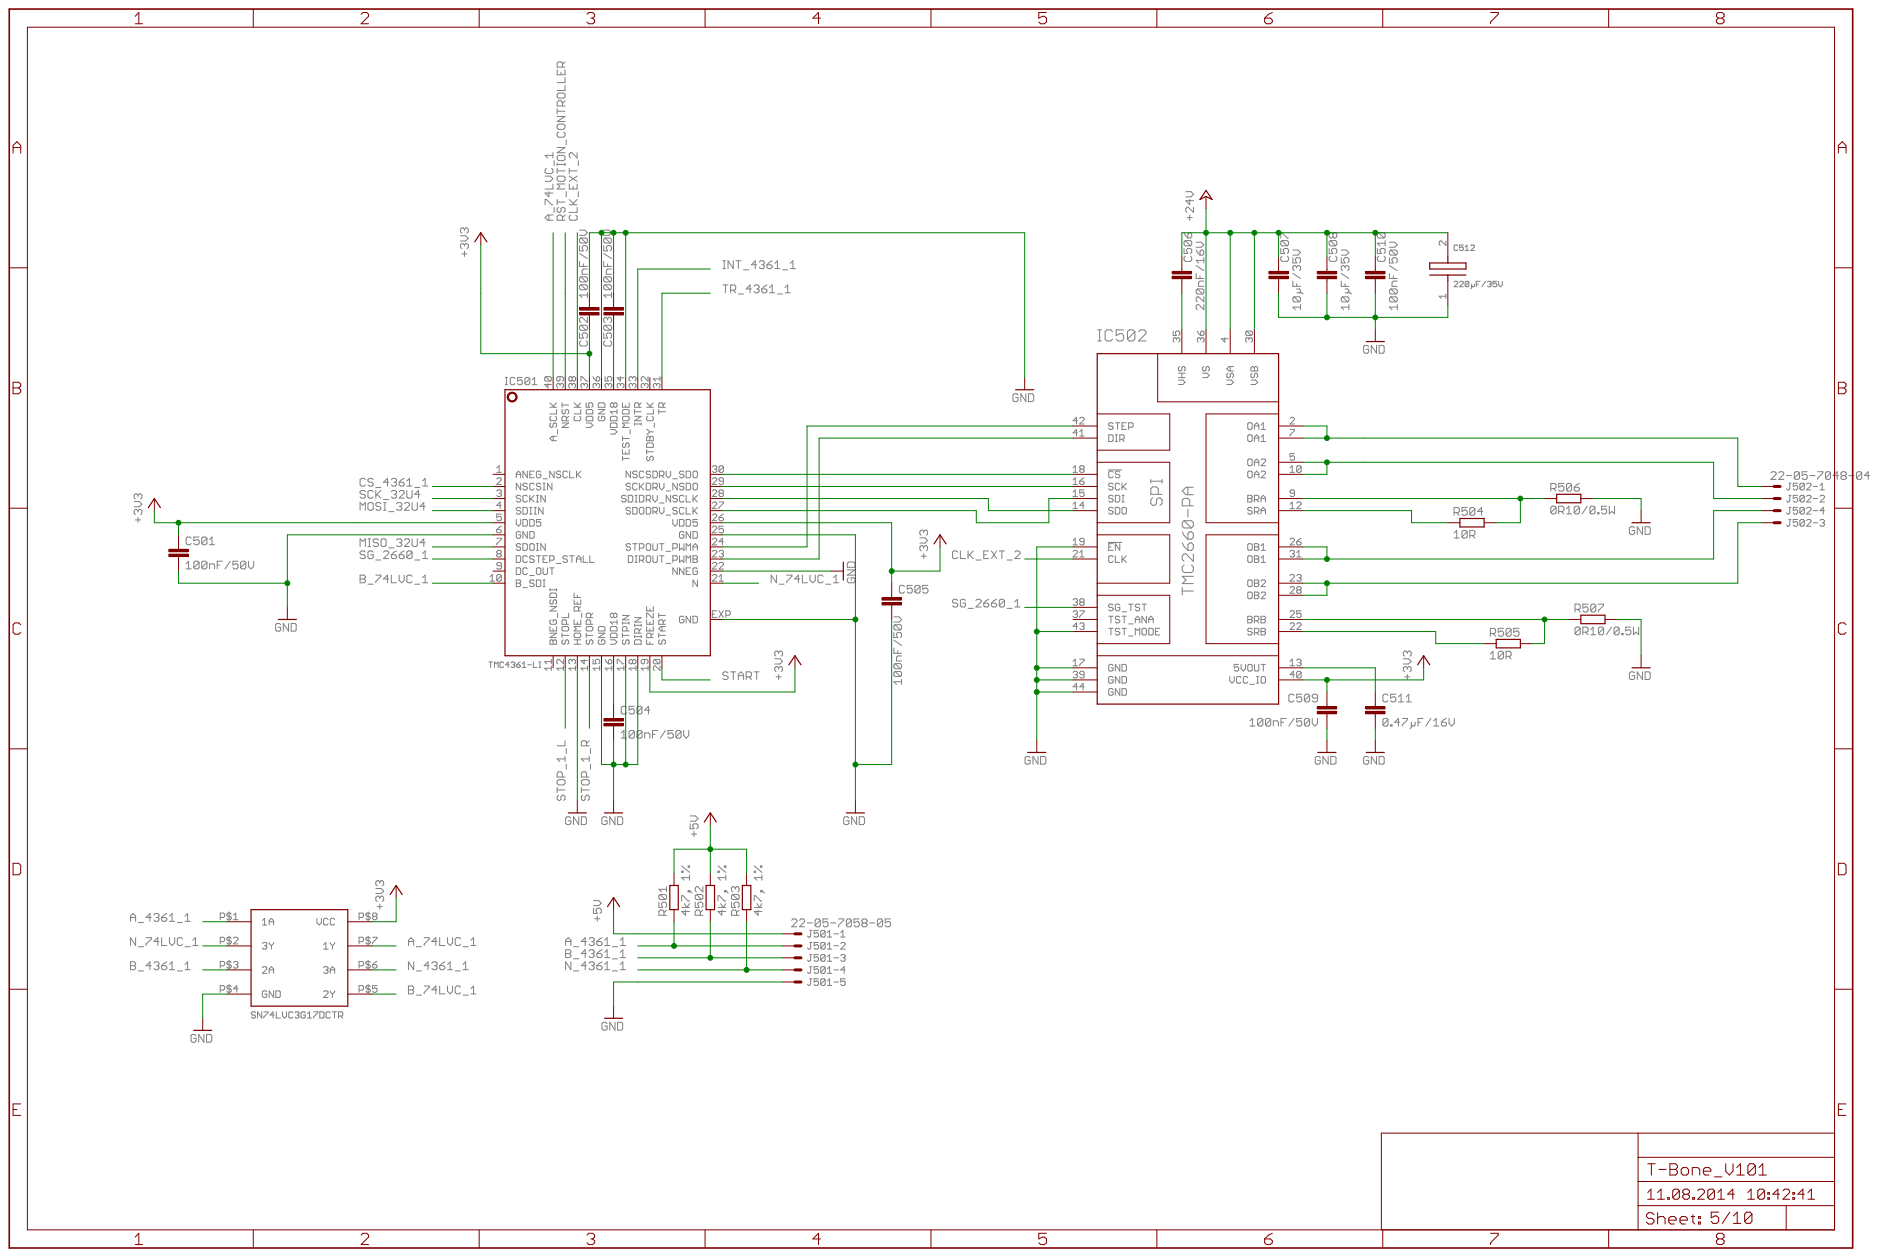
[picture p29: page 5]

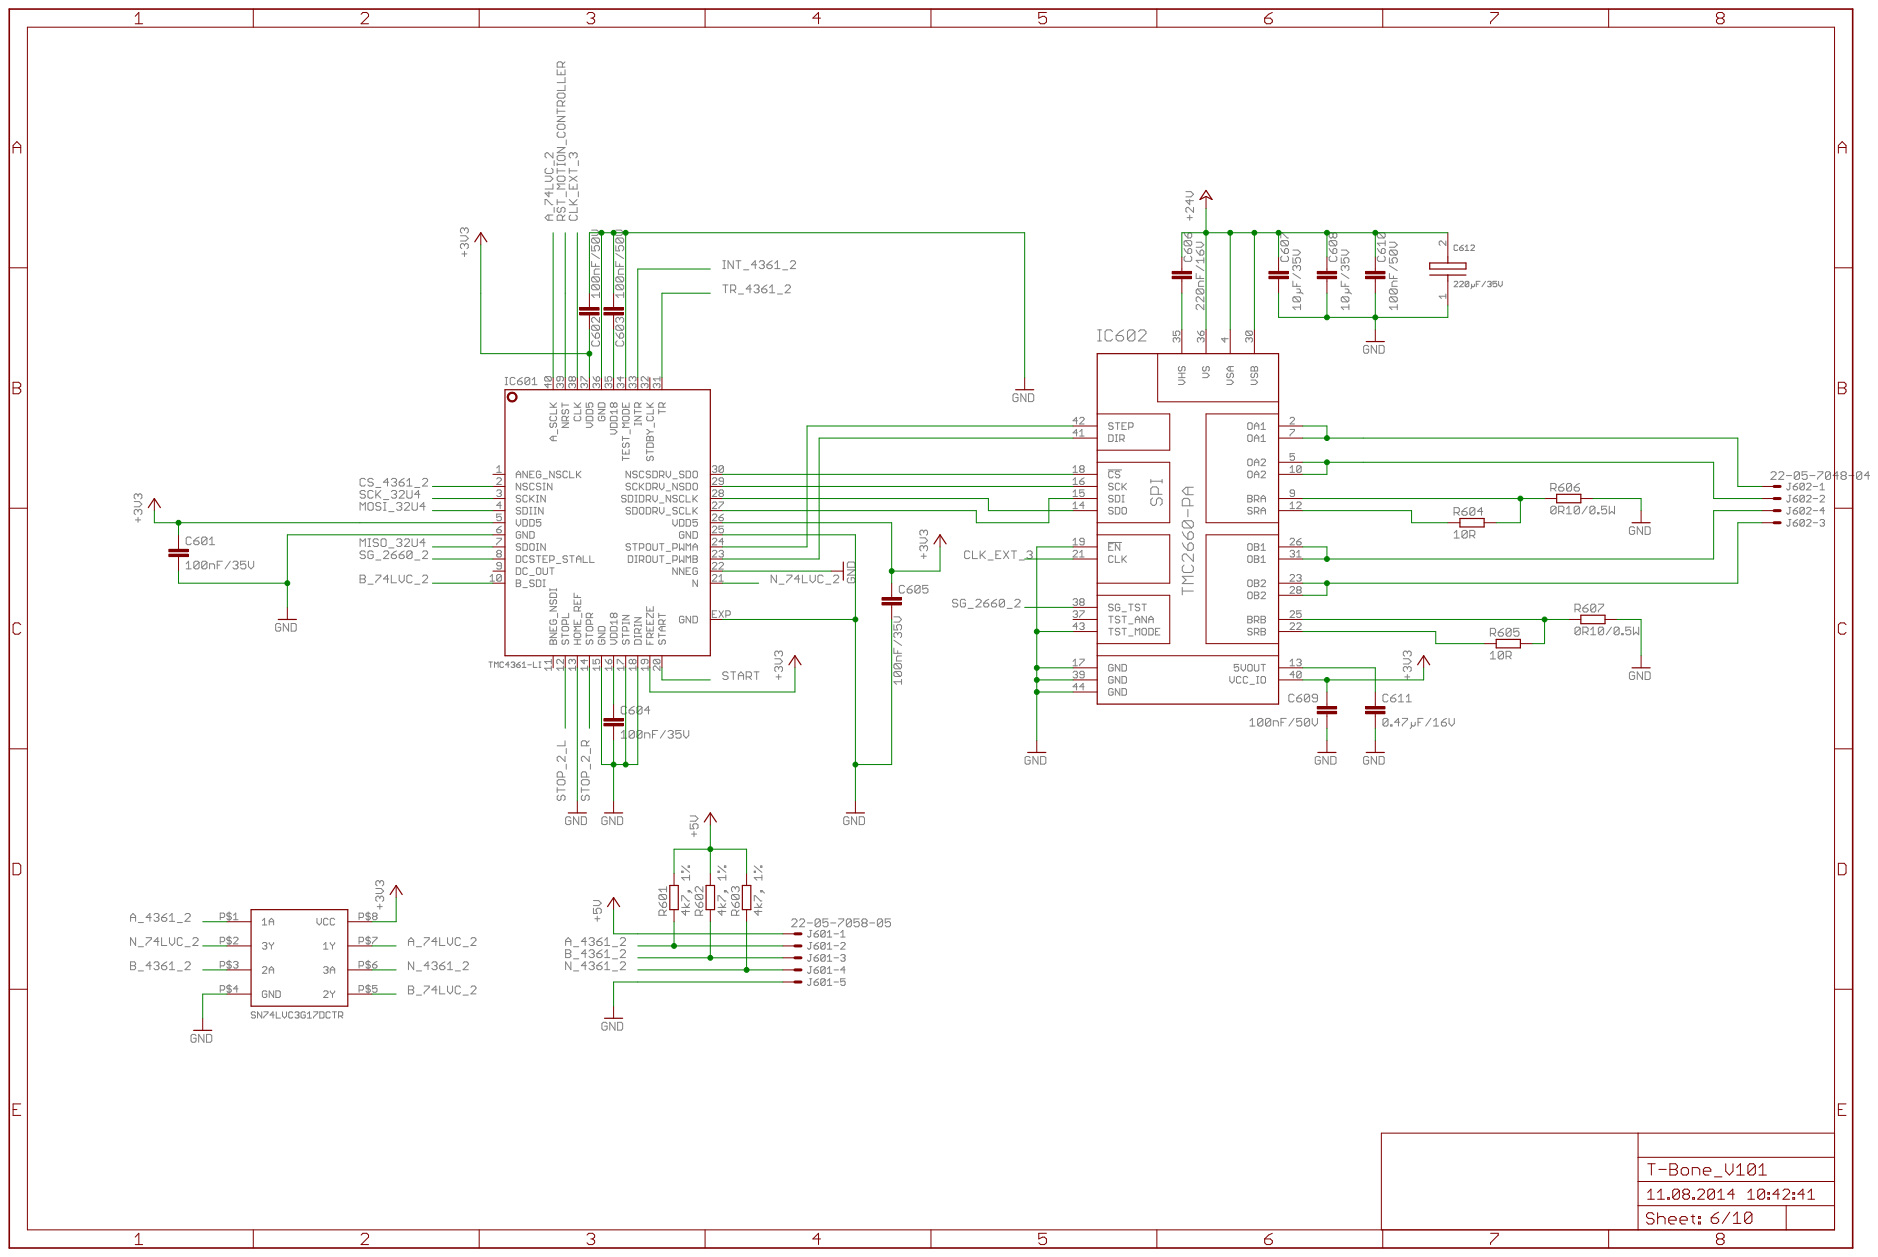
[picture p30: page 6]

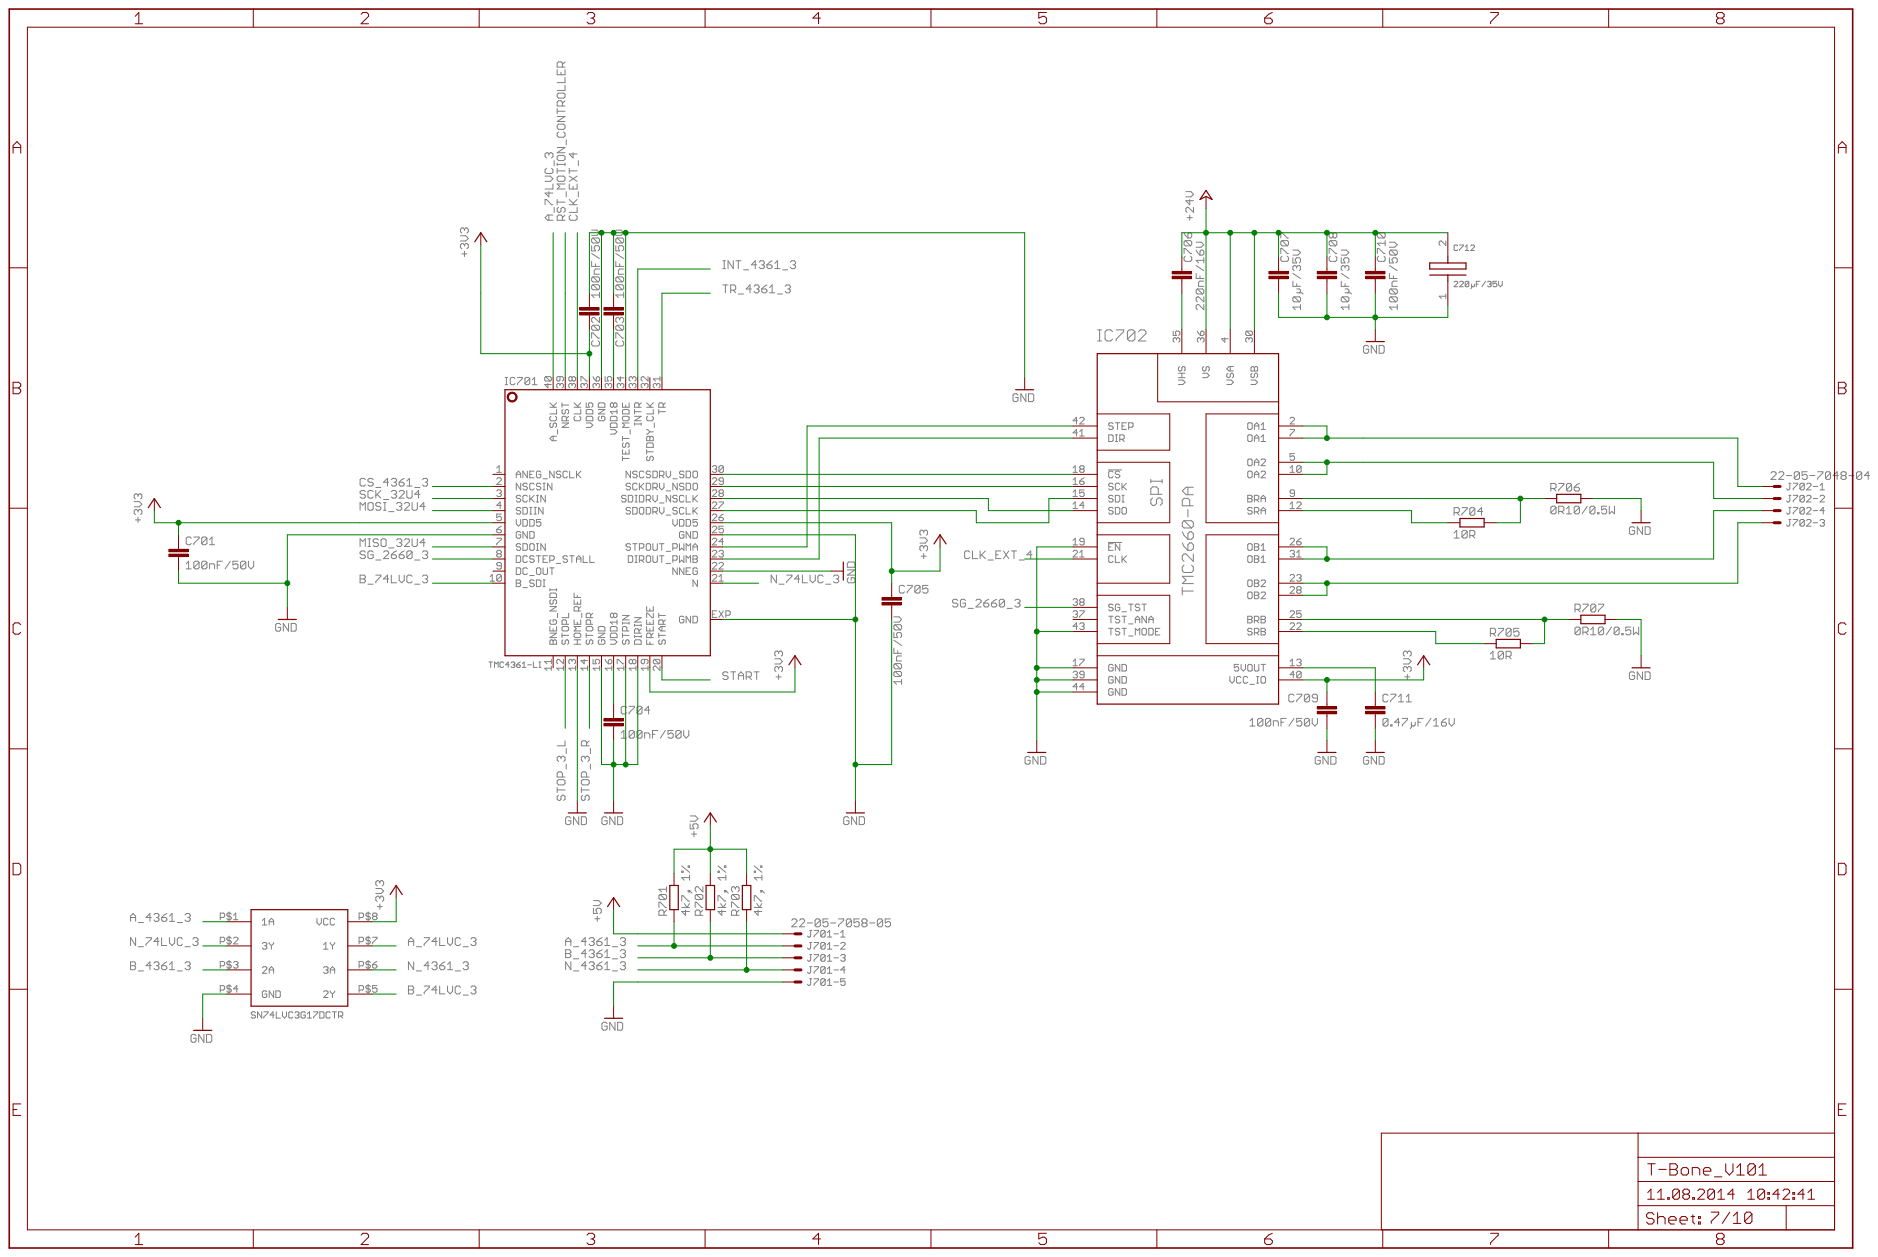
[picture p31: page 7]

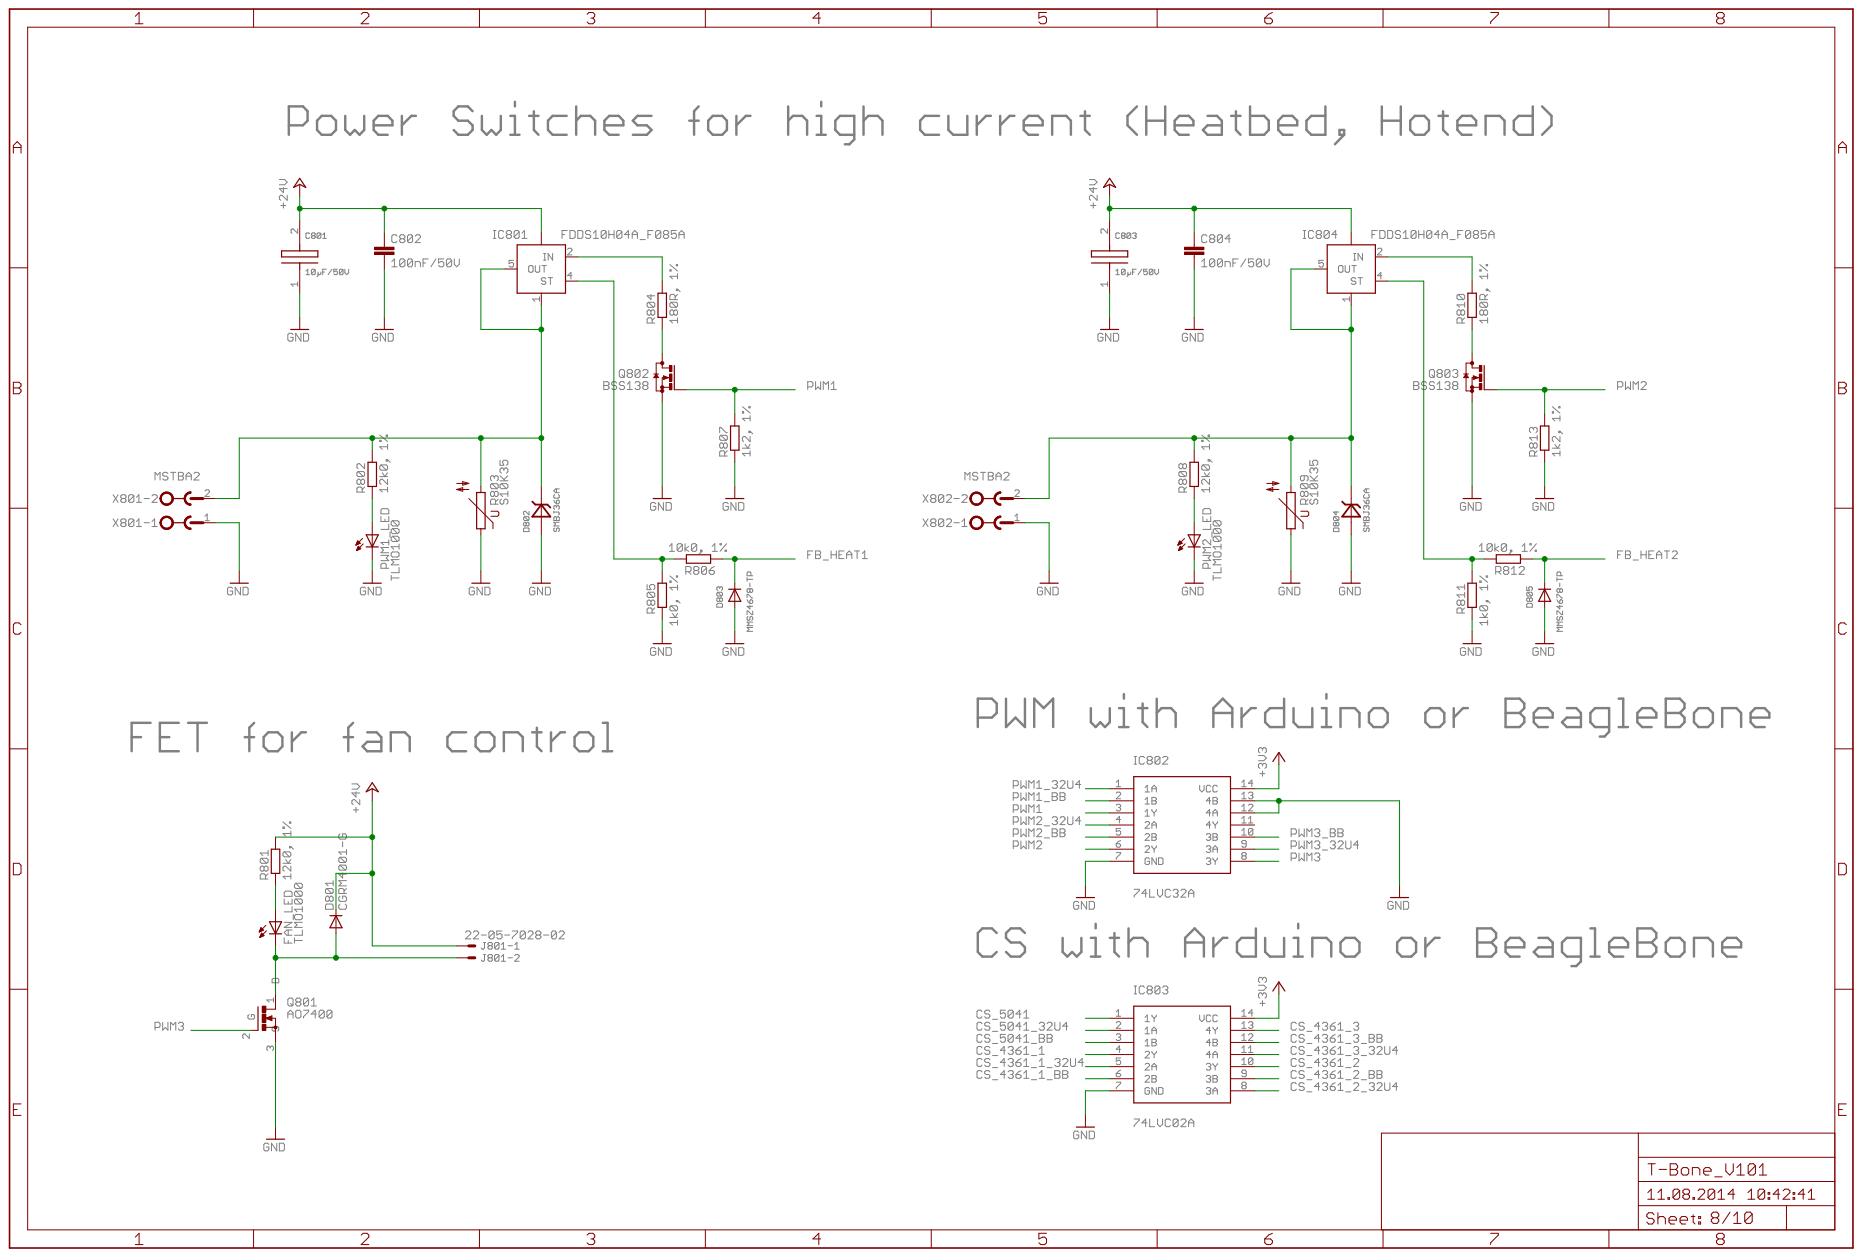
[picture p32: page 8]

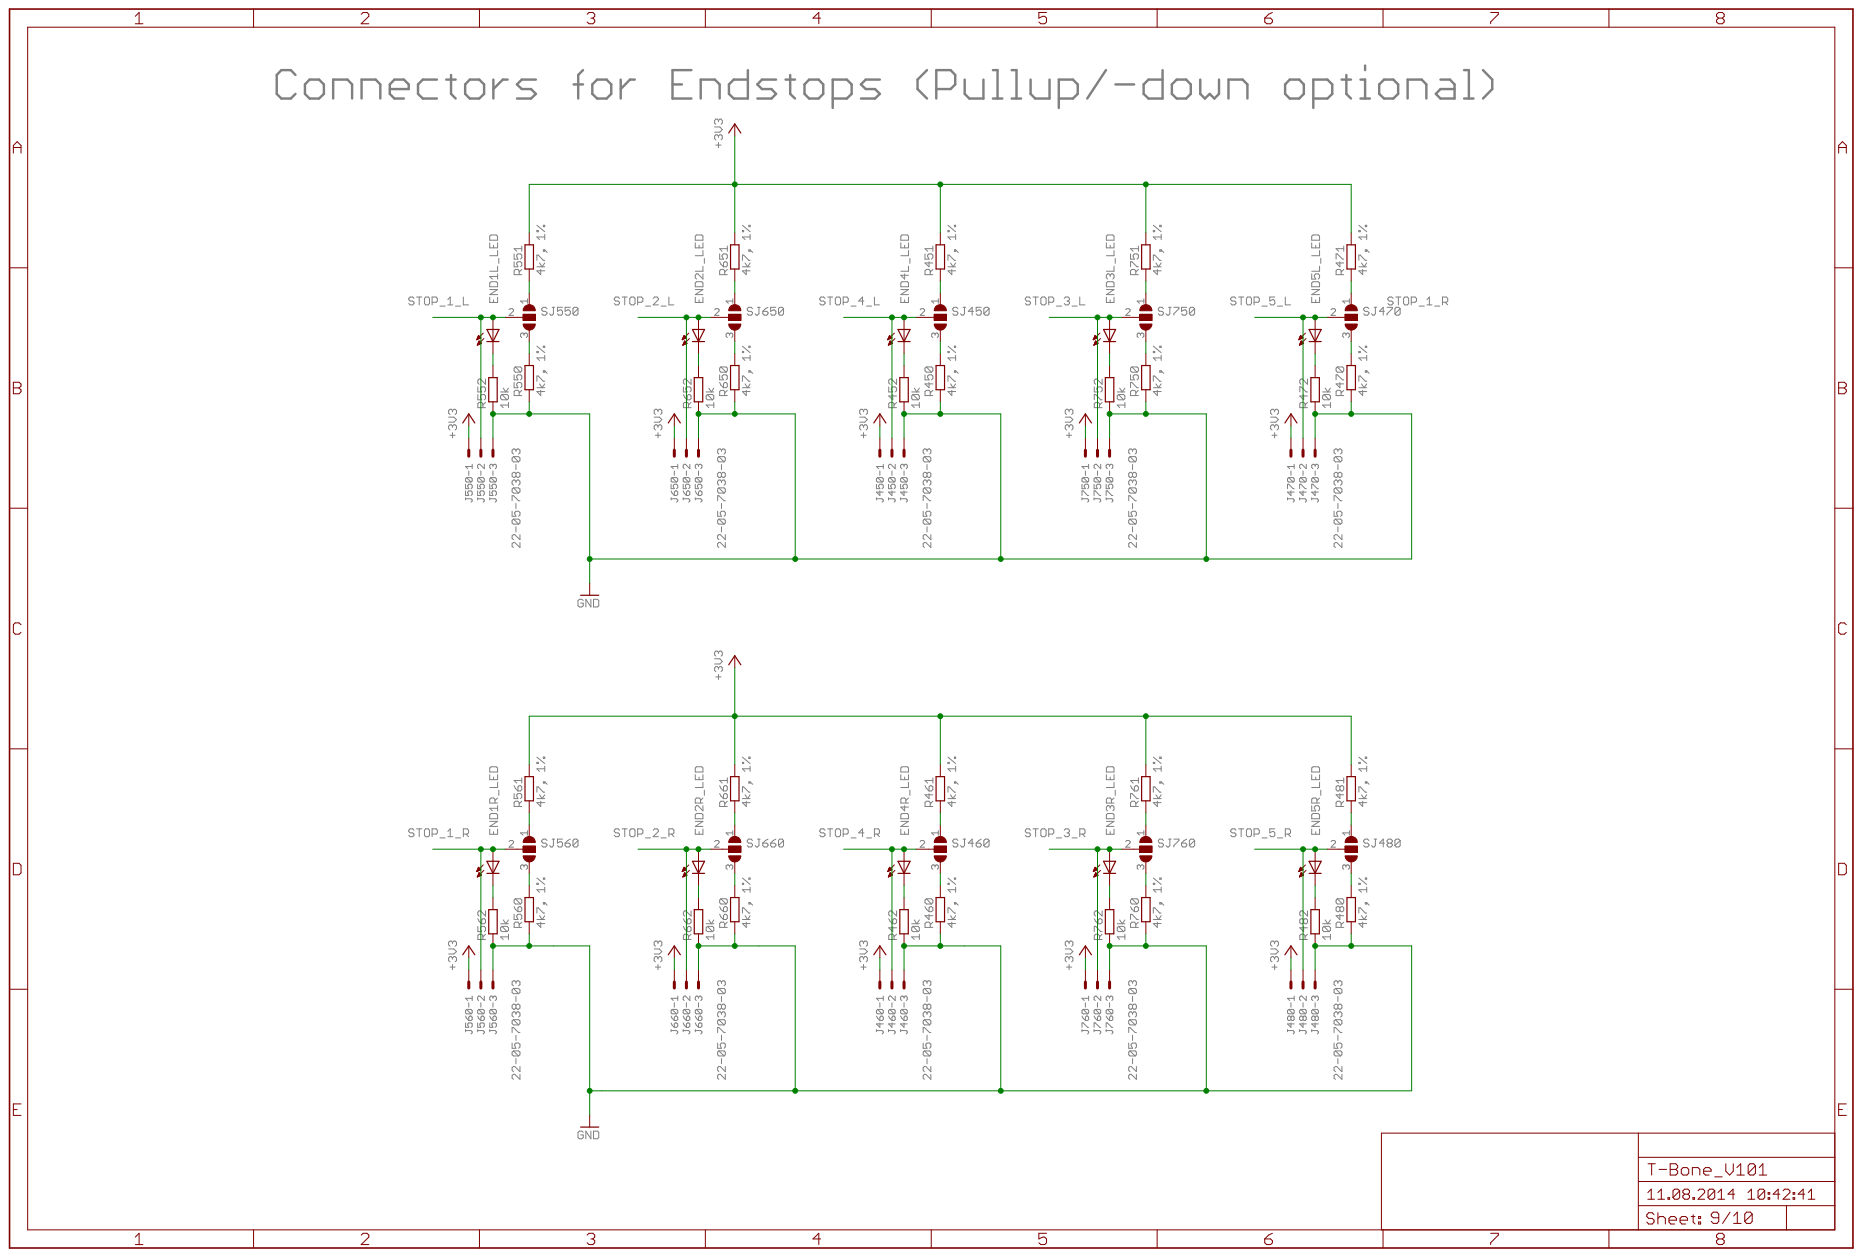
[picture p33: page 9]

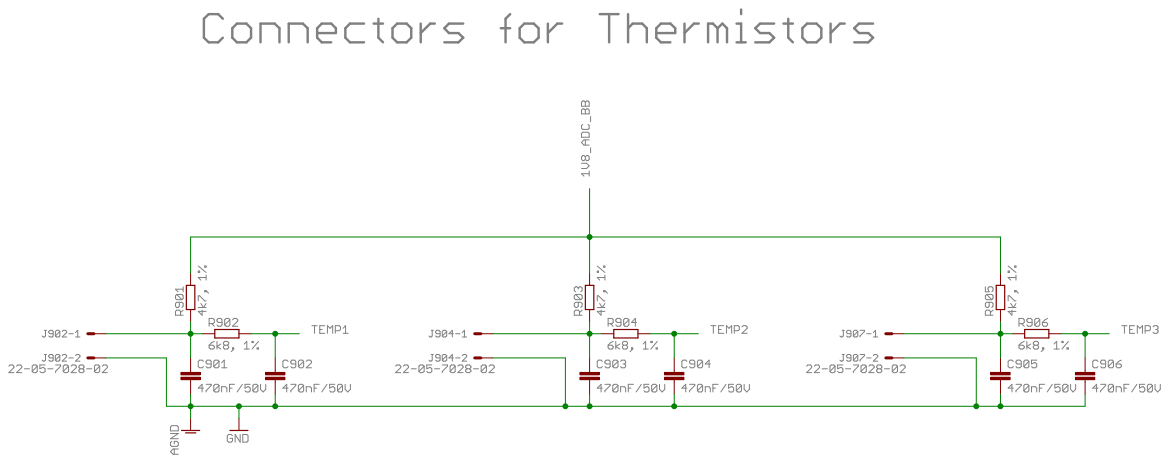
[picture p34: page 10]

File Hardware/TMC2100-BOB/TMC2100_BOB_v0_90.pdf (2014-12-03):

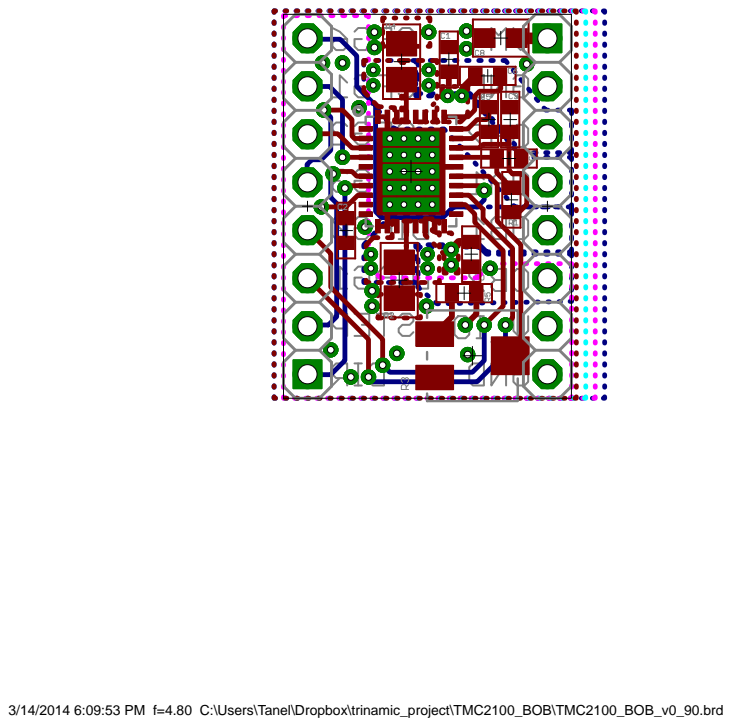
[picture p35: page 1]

3/14/2014 6:09:53 PM f=4.80 C:\Users\Tanel\Dropbox\trinamic_project\TMC2100_BOB\TMC2100_BOB_v0_90.brd



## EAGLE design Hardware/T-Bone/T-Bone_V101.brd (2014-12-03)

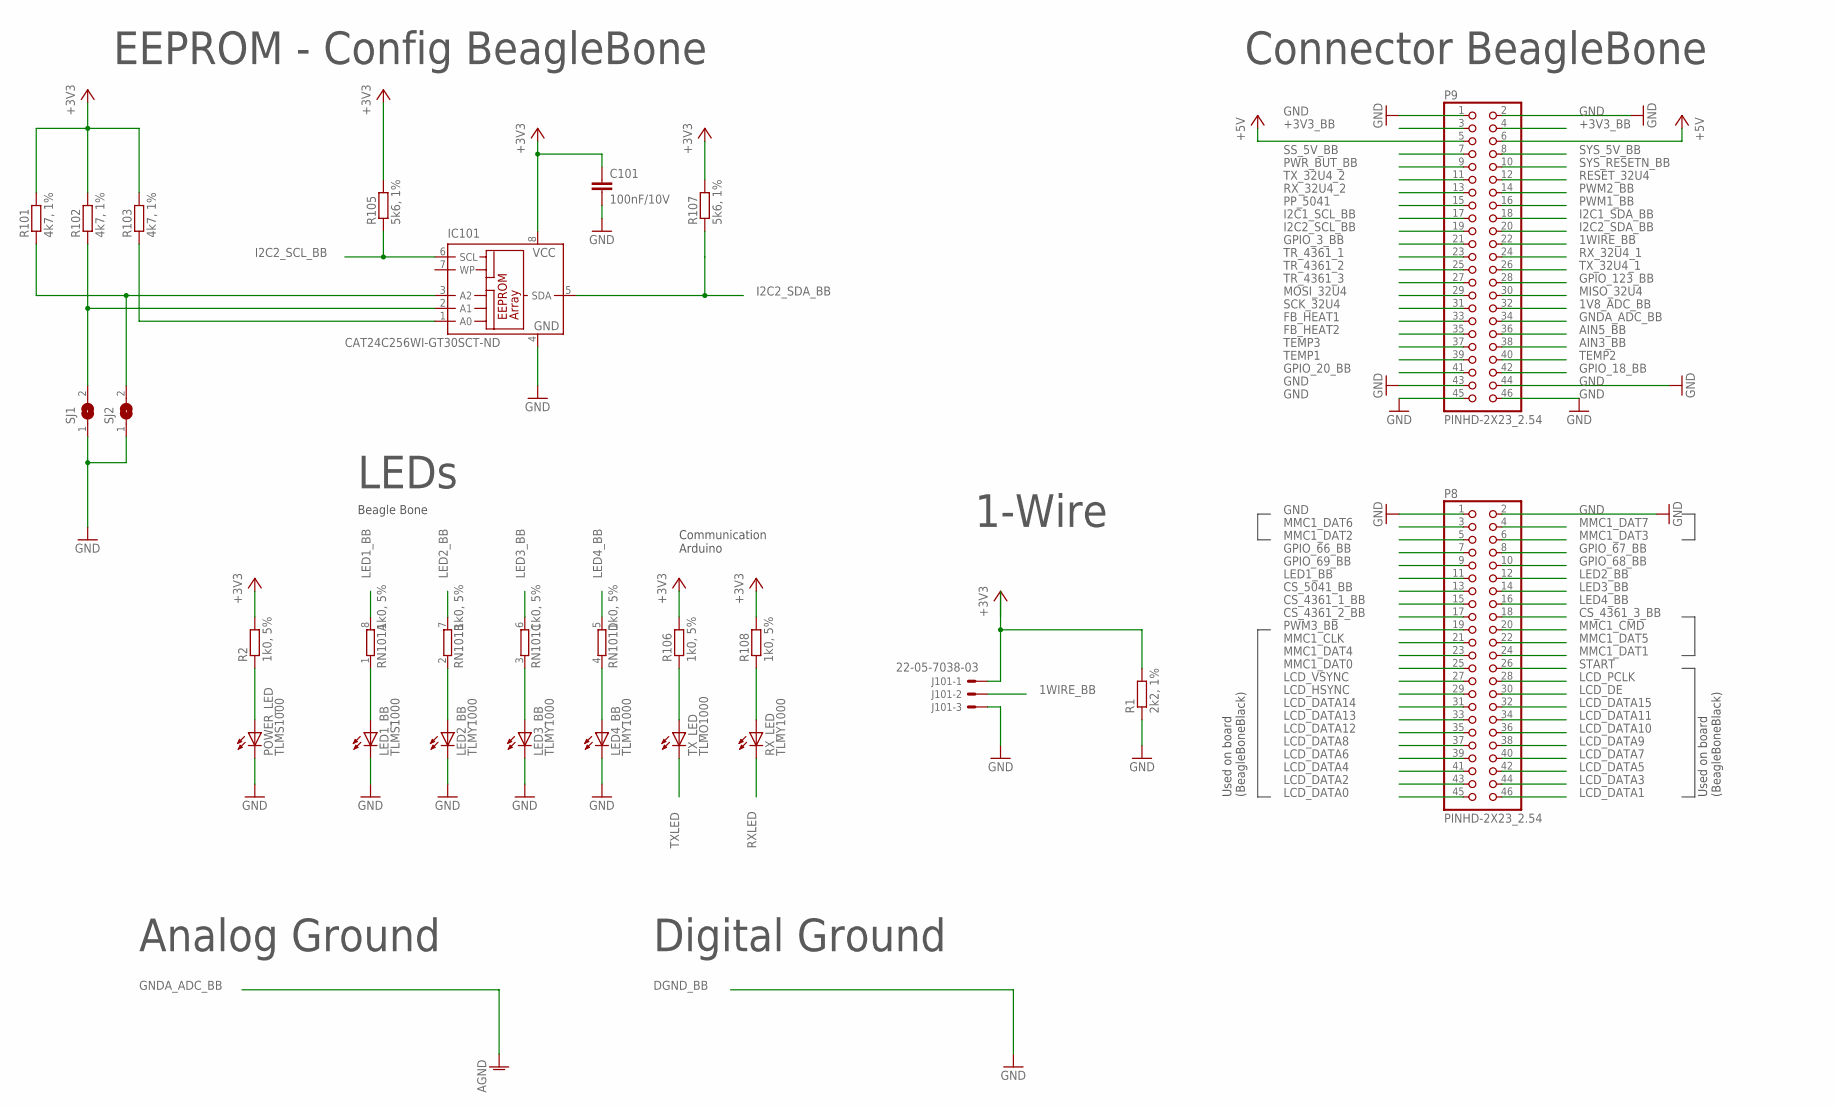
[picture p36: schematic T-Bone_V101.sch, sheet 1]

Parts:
C101: 100nF/10V; C0402K
IC101: CAT24C256WI-GT30SCT-ND; SO-08
J101: 22-05-7038-03; 7395-03
LED1_BB: TLMS1000; CHIP-LED0603
LED2_BB, LED3_BB, LED4_BB: TLMY1000; CHIP-LED0603
P8, P9: PINHD-2X23_2.54; 2X23
POWER_LED: TLMS1000; CHIP-LED0603
R1: 2k2, 1%; R0603
R2, R106, R108: 1k0, 5%; R0402
R101, R102, R103: 4k7, 1%; R0402
R105, R107: 5k6, 1%; R0402
RN101: 1k0, 5%; YC124
RX_LED: TLMY1000; CHIP-LED0603
SJ1, SJ2: SJ
TX_LED: TLMO1000; CHIP-LED0603

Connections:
1V8_ADC_BB: P9.32; also elsewhere on the board
1WIRE_BB: J101.2, P9.22
+3V3: C101.1, IC101.8 (VCC), J101.1, R1.2, R2.2, R101.2, R102.2, R103.2, R105.2, R106.2, R107.2, R108.2; also elsewhere on the board
+3V3_BB: P9.3, P9.4
+5V: P9.5, P9.6; also elsewhere on the board
AIN3_BB: P9.38
AIN5_BB: P9.36
CS_4361_1_BB: P8.15; also elsewhere on the board
CS_4361_2_BB: P8.17; also elsewhere on the board
CS_4361_3_BB: P8.18; also elsewhere on the board
CS_5041_BB: P8.13; also elsewhere on the board
FB_HEAT1: P9.33; also elsewhere on the board
FB_HEAT2: P9.35; also elsewhere on the board
GND: C101.2, IC101.4 (GND), J101.3, LED1_BB.C, LED2_BB.C, LED3_BB.C, LED4_BB.C, P8.1, P8.2, P9.1, P9.2, P9.43, P9.44, P9.45, P9.46, POWER_LED.C, R1.1, SJ1.1, SJ2.1; also elsewhere on the board
GNDA_ADC_BB: P9.34
GPIO_3_BB: P9.21
GPIO_18_BB: P9.42
GPIO_20_BB: P9.41
GPIO_66_BB: P8.7
GPIO_67_BB: P8.8
GPIO_68_BB: P8.10
GPIO_69_BB: P8.9
GPIO_123_BB: P9.28
I2C1_SCL_BB: P9.17
I2C1_SDA_BB: P9.18
I2C2_SCL_BB: IC101.6 (SCL), P9.19, R105.1
I2C2_SDA_BB: IC101.5 (SDA), P9.20, R107.1
LCD_DATA0: P8.45
LCD_DATA1: P8.46
LCD_DATA2: P8.43
LCD_DATA3: P8.44
LCD_DATA4: P8.41
LCD_DATA5: P8.42
LCD_DATA6: P8.39
LCD_DATA7: P8.40
LCD_DATA8: P8.37
LCD_DATA9: P8.38
LCD_DATA10: P8.36
LCD_DATA11: P8.34
LCD_DATA12: P8.35
LCD_DATA13: P8.33
LCD_DATA14: P8.31
LCD_DATA15: P8.32
LCD_DE: P8.30
LCD_HSYNC: P8.29
LCD_PCLK: P8.28
LCD_VSYNC: P8.27
LED1_BB: P8.11, RN101.8 (2)
LED2_BB: P8.12, RN101.7 (2)
LED3_BB: P8.14, RN101.6 (2)
LED4_BB: P8.16, RN101.5 (2)
MISO_32U4: P9.30; also elsewhere on the board
MMC1_CLK: P8.21
MMC1_CMD: P8.20
MMC1_DAT0: P8.25
MMC1_DAT1: P8.24
MMC1_DAT2: P8.5
MMC1_DAT3: P8.6
MMC1_DAT4: P8.23
MMC1_DAT5: P8.22
MMC1_DAT6: P8.3
MMC1_DAT7: P8.4
MOSI_32U4: P9.29; also elsewhere on the board
unnamed: R106.1, TX_LED.A
unnamed: R108.1, RX_LED.A
unnamed: POWER_LED.A, R2.1
unnamed: LED1_BB.A, RN101.1
unnamed: LED2_BB.A, RN101.2 (1)
unnamed: LED3_BB.A, RN101.3 (1)
unnamed: LED4_BB.A, RN101.4 (1)
unnamed: IC101.2 (A1), R102.1, SJ1.2
unnamed: IC101.1 (A0), R103.1
unnamed: IC101.3 (A2), R101.1, SJ2.2
PP_5041: P9.15; also elsewhere on the board
PWM1_BB: P9.16; also elsewhere on the board
PWM2_BB: P9.14; also elsewhere on the board
PWM3_BB: P8.19; also elsewhere on the board
PWR_BUT_BB: P9.9
RESET_32U4: P9.12; also elsewhere on the board
RXLED: RX_LED.C; also elsewhere on the board
RX_32U4_1: P9.24; also elsewhere on the board
RX_32U4_2: P9.13; also elsewhere on the board
SCK_32U4: P9.31; also elsewhere on the board
SS_5V_BB: P9.7
START: P8.26; also elsewhere on the board
SYS_5V_BB: P9.8
SYS_RESETN_BB: P9.10
TEMP1: P9.39; also elsewhere on the board
TEMP2: P9.40; also elsewhere on the board
TEMP3: P9.37; also elsewhere on the board
TR_4361_1: P9.23; also elsewhere on the board
TR_4361_2: P9.25; also elsewhere on the board
TR_4361_3: P9.27; also elsewhere on the board
TXLED: TX_LED.C; also elsewhere on the board
TX_32U4_1: P9.26; also elsewhere on the board
TX_32U4_2: P9.11; also elsewhere on the board

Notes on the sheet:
EEPROM - Config BeagleBone
Connector BeagleBone
Analog Ground
Digital Ground
LEDs
1-Wire
Communication Arduino
Beagle Bone
Used on board (BeagleBoneBlack)

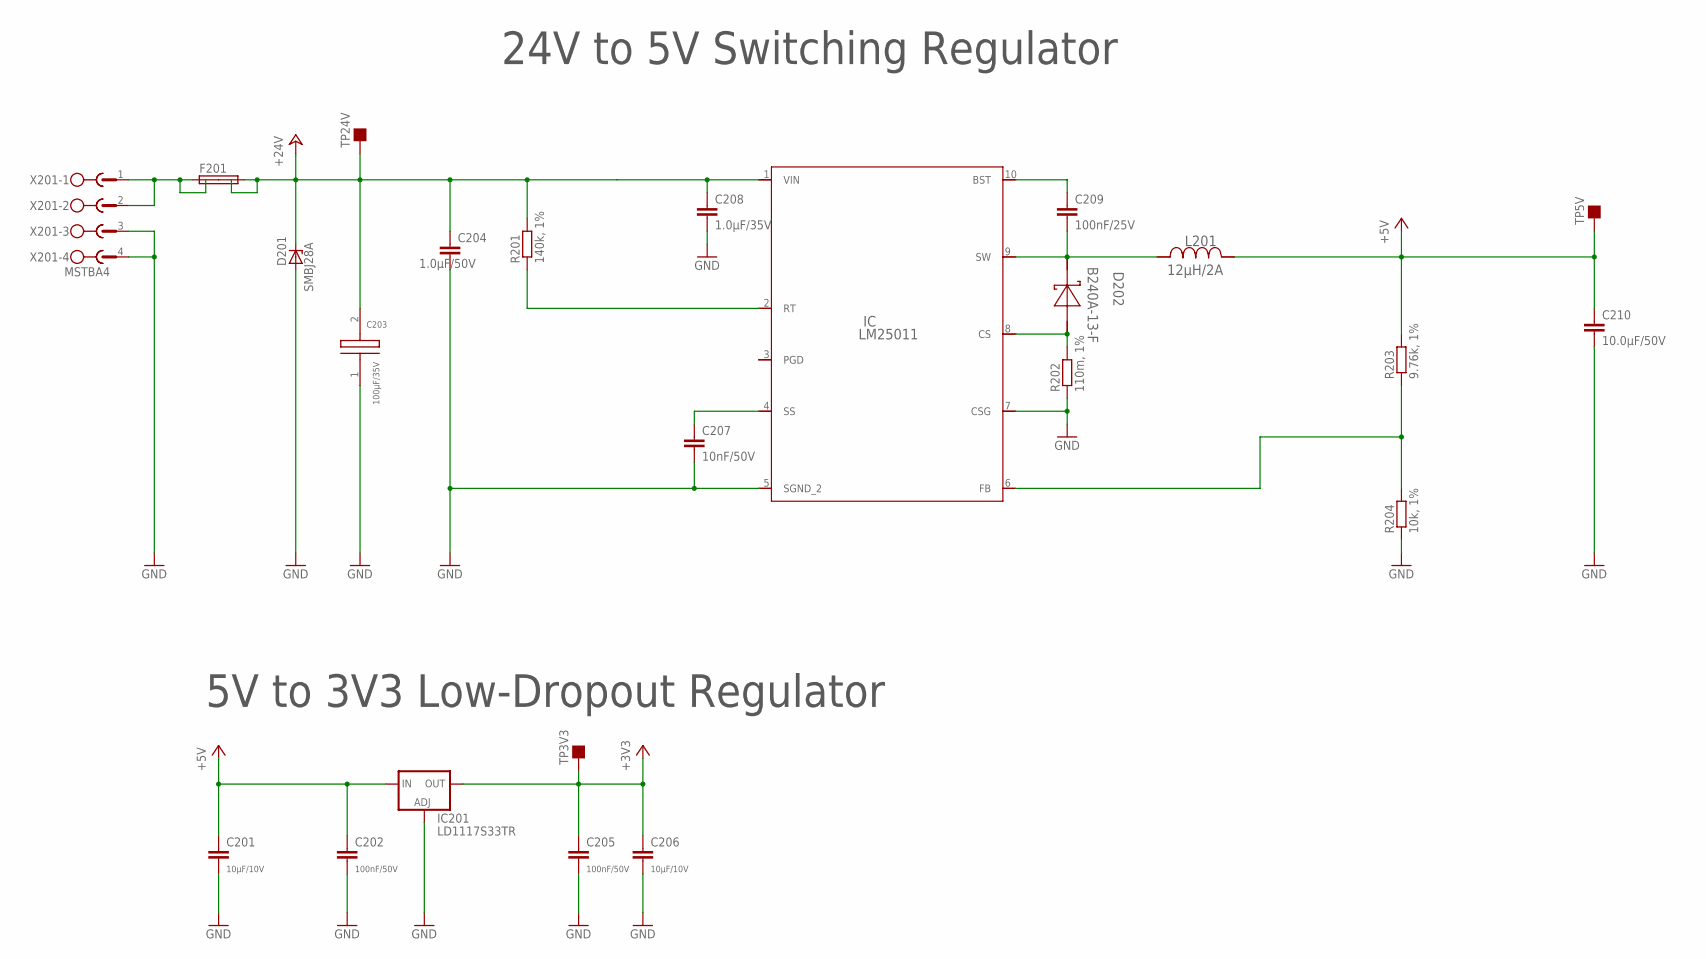
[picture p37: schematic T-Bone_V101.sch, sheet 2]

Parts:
C201, C206: 10µF/10V; C0805K
C202, C205: 100nF/50V; C0603K
C203: 100µF/35V; F
C204: 1.0µF/50V; C1206K
C207: 10nF/50V; C0805K
C208: 1.0µF/35V; C0805K
C209: 100nF/25V; C0805K
C210: 10.0µF/50V; C0603K
D201: SMBJ28A; SMB
D202: B240A-13-F; SMA
F201: SHK20Q
IC: LM25011; MUC10A
IC201: LD1117S33TR; SOT223
L201: 12µH/2A; SDR0805
R201: 140k, 1%; R0402
R202: 110m, 1%; R1210
R203: 9.76k, 1%; R0402
R204: 10k, 1%; R0402
TP3V3, TP5V, TP24V: TP
X201: MSTBA4

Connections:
24V_INPUT: F201.1A, F201.1B, X201.1, X201.2
+3V3: C205.1, C206.1, IC201.4 (OUT), TP3V3.P$1; also elsewhere on the board
+5V: C201.1, C202.1, C210.1, IC201.3 (IN), L201.1, R203.2, TP5V.P$1; also elsewhere on the board
+24V: C203.2, C204.1, C208.1, D201.C, F201.2A, F201.2B, IC.1 (VIN), R201.2, TP24V.P$1; also elsewhere on the board
GND: C201.2, C202.2, C203.1, C204.2, C205.2, C206.2, C207.2, C208.2, C210.2, D201.A, IC.5 (SGND_2), IC.7 (CSG), IC201.1 (ADJ), R202.1, R204.1, X201.3, X201.4; also elsewhere on the board
unnamed: D202.2 (A), IC.8 (CS), R202.2
unnamed: C209.2, D202.1 (K), IC.9 (SW), L201.2
unnamed: IC.6 (FB), R203.1, R204.2
unnamed: C209.1, IC.10 (BST)
unnamed: C207.1, IC.4 (SS)
unnamed: IC.2 (RT), R201.1

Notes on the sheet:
24V to 5V Switching Regulator
5V to 3V3 Low-Dropout Regulator

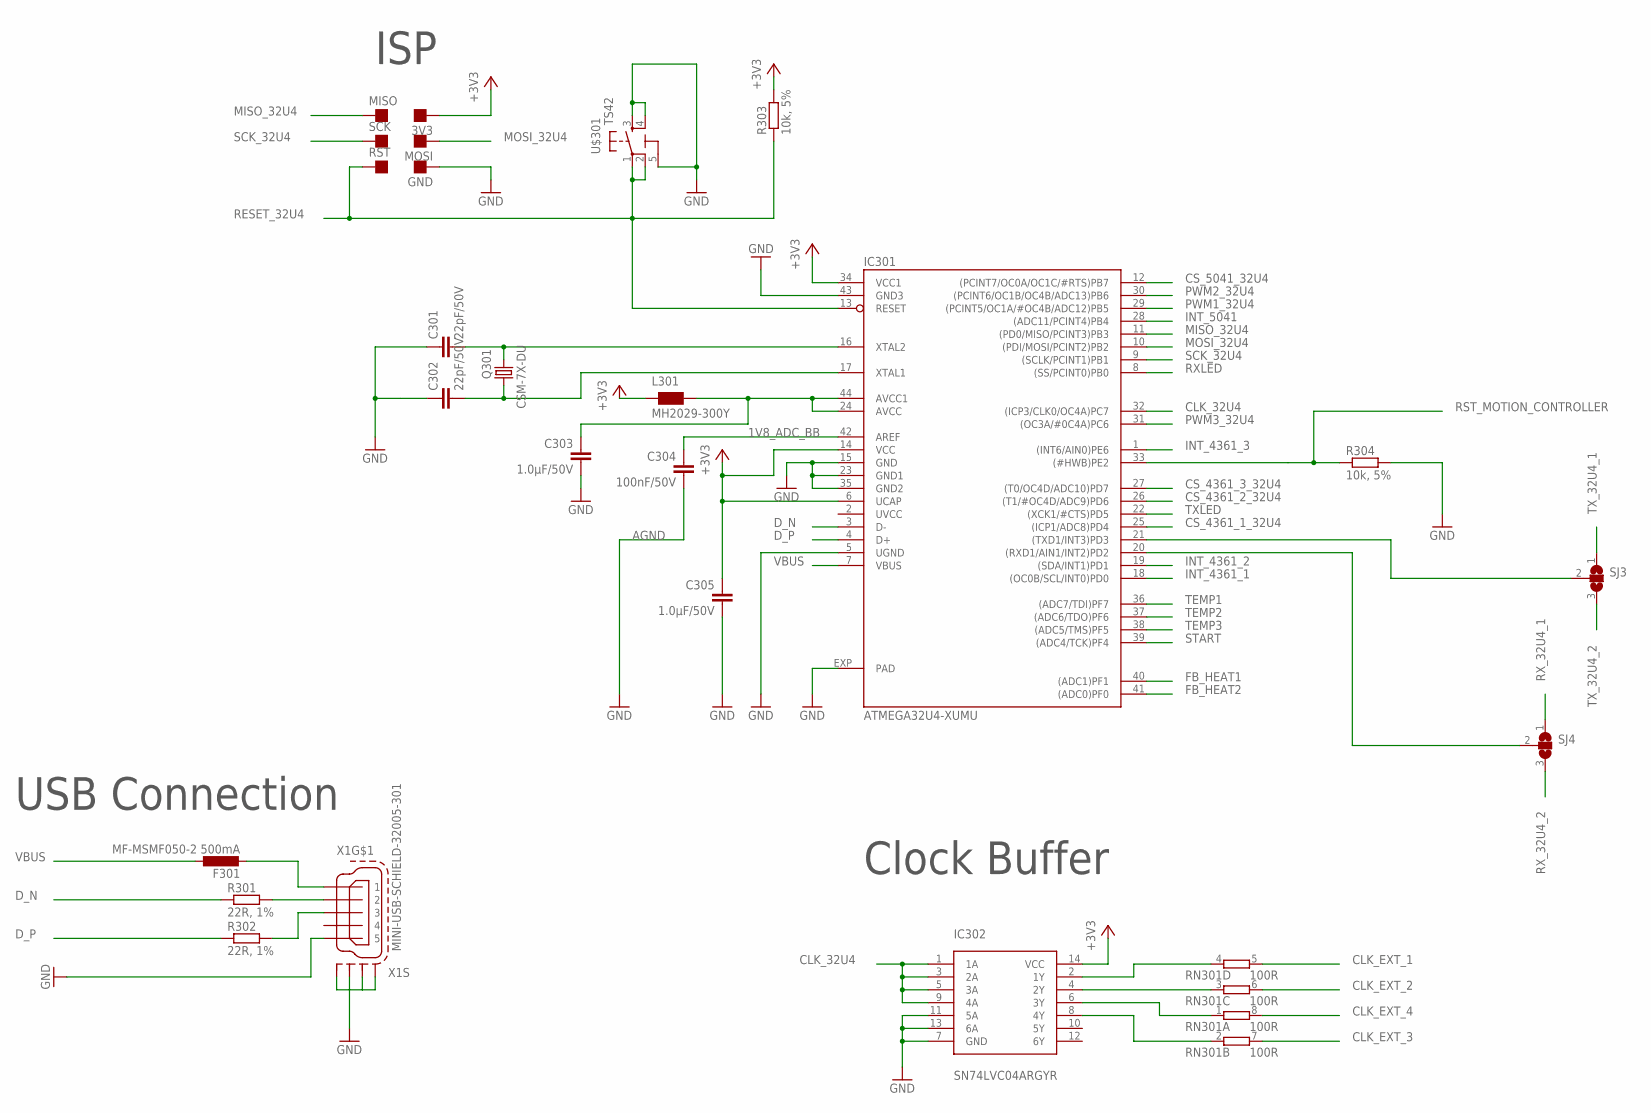
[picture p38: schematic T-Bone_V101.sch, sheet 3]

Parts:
3V3: TP
C301, C302: 22pF/50V; C0603K
C303, C305: 1.0µF/50V; C0603K
C304: 100nF/50V; C0603K
F301: MF-MSMF050-2 500mA; L1812
GND: TP
IC301: ATMEGA32U4-XUMU; QFN44ML7X7
IC302: SN74LVC04ARGYR; 14-VFQFN
L301: MH2029-300Y; 0805
MISO: TP
MOSI: TP
Q301: CSM-7X-DU
R301, R302: 22R, 1%; R0402
R303: 10k, 5%; R0603
R304: 10k, 5%; R0402
RN301: 100R; YC124
RST: TP
SCK: TP
SJ3, SJ4: SJ2W; SJ_2
U$301: TS42
X1: MINI-USB-SCHIELD-32005-301; 32005-301

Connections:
1V8_ADC_BB: C304.1, IC301.42 (AREF); also elsewhere on the board
+3V3: 3V3.P$1, C305.1, IC301.6 (UCAP), IC301.14 (VCC), IC301.34 (VCC1), IC302.14 (VCC), L301.1, R303.2; also elsewhere on the board
AGND: C304.2
CLK_32U4: IC301.32 ((ICP3/CLK0/OC4A)PC7), IC302.1 (1A), IC302.3 (2A), IC302.5 (3A), IC302.9 (4A)
CLK_EXT_1: RN301.5 (2); also elsewhere on the board
CLK_EXT_2: RN301.6 (2); also elsewhere on the board
CLK_EXT_3: RN301.7 (2); also elsewhere on the board
CLK_EXT_4: RN301.8 (2); also elsewhere on the board
CS_4361_1_32U4: IC301.25 ((ICP1/ADC8)PD4); also elsewhere on the board
CS_4361_2_32U4: IC301.26 ((T1/#OC4D/ADC9)PD6); also elsewhere on the board
CS_4361_3_32U4: IC301.27 ((T0/OC4D/ADC10)PD7); also elsewhere on the board
CS_5041_32U4: IC301.12 ((PCINT7/OC0A/OC1C/#RTS)PB7); also elsewhere on the board
D_N: IC301.3 (D-), R301.1
D_P: IC301.4 (D+), R302.1
FB_HEAT1: IC301.40 ((ADC1)PF1); also elsewhere on the board
FB_HEAT2: IC301.41 ((ADC0)PF0); also elsewhere on the board
GND: C301.1, C302.1, C303.2, C305.2, GND.P$1, IC301.5 (UGND), IC301.15 (GND), IC301.23 (GND1), IC301.35 (GND2), IC301.43 (GND3), IC301.EXP (PAD), IC302.7 (GND), IC302.11 (5A), IC302.13 (6A), R304.2, U$301.3, U$301.4, U$301.5 (5-GND), X1.5, X1.M1 (S1), X1.M2 (S2), X1.M3 (S3), X1.M4 (S4); also elsewhere on the board
INT_4361_1: IC301.18 ((OC0B/SCL/INT0)PD0); also elsewhere on the board
INT_4361_2: IC301.19 ((SDA/INT1)PD1); also elsewhere on the board
INT_4361_3: IC301.1 ((INT6/AIN0)PE6); also elsewhere on the board
INT_5041: IC301.28 ((ADC11/PCINT4)PB4); also elsewhere on the board
MISO_32U4: IC301.11 ((PD0/MISO/PCINT3)PB3), MISO.P$1; also elsewhere on the board
MOSI_32U4: IC301.10 ((PDI/MOSI/PCINT2)PB2), MOSI.P$1; also elsewhere on the board
unnamed: IC301.21 ((TXD1/INT3)PD3), SJ3.2
unnamed: R302.2, X1.3
unnamed: R301.2, X1.2
unnamed: IC302.6 (3Y), RN301.1
unnamed: IC302.8 (4Y), RN301.2 (1)
unnamed: IC302.2 (1Y), RN301.4 (1)
unnamed: C303.1, IC301.24 (AVCC), IC301.44 (AVCC1), L301.2
unnamed: IC302.4 (2Y), RN301.3 (1)
unnamed: F301.2, X1.1
unnamed: C301.2, IC301.16 (XTAL2), Q301.2
unnamed: C302.2, IC301.17 (XTAL1), Q301.1
unnamed: IC301.20 ((RXD1/AIN1/INT2)PD2), SJ4.2
PWM1_32U4: IC301.29 ((PCINT5/OC1A/#OC4B/ADC12)PB5); also elsewhere on the board
PWM2_32U4: IC301.30 ((PCINT6/OC1B/OC4B/ADC13)PB6); also elsewhere on the board
PWM3_32U4: IC301.31 ((OC3A/#0C4A)PC6); also elsewhere on the board
RESET_32U4: IC301.13 (RESET), R303.1, RST.P$1, U$301.1, U$301.2; also elsewhere on the board
RST_MOTION_CONTROLLER: IC301.33 ((#HWB)PE2), R304.1; also elsewhere on the board
RXLED: IC301.8 ((SS/PCINT0)PB0); also elsewhere on the board
RX_32U4_1: SJ4.1; also elsewhere on the board
RX_32U4_2: SJ4.3; also elsewhere on the board
SCK_32U4: IC301.9 ((SCLK/PCINT1)PB1), SCK.P$1; also elsewhere on the board
START: IC301.39 ((ADC4/TCK)PF4); also elsewhere on the board
TEMP1: IC301.36 ((ADC7/TDI)PF7); also elsewhere on the board
TEMP2: IC301.37 ((ADC6/TDO)PF6); also elsewhere on the board
TEMP3: IC301.38 ((ADC5/TMS)PF5); also elsewhere on the board
TXLED: IC301.22 ((XCK1/#CTS)PD5); also elsewhere on the board
TX_32U4_1: SJ3.1; also elsewhere on the board
TX_32U4_2: SJ3.3; also elsewhere on the board
UVCC: IC301.2 (UVCC)
VBUS: F301.1, IC301.7 (VBUS)

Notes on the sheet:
ISP
USB Connection
Clock Buffer

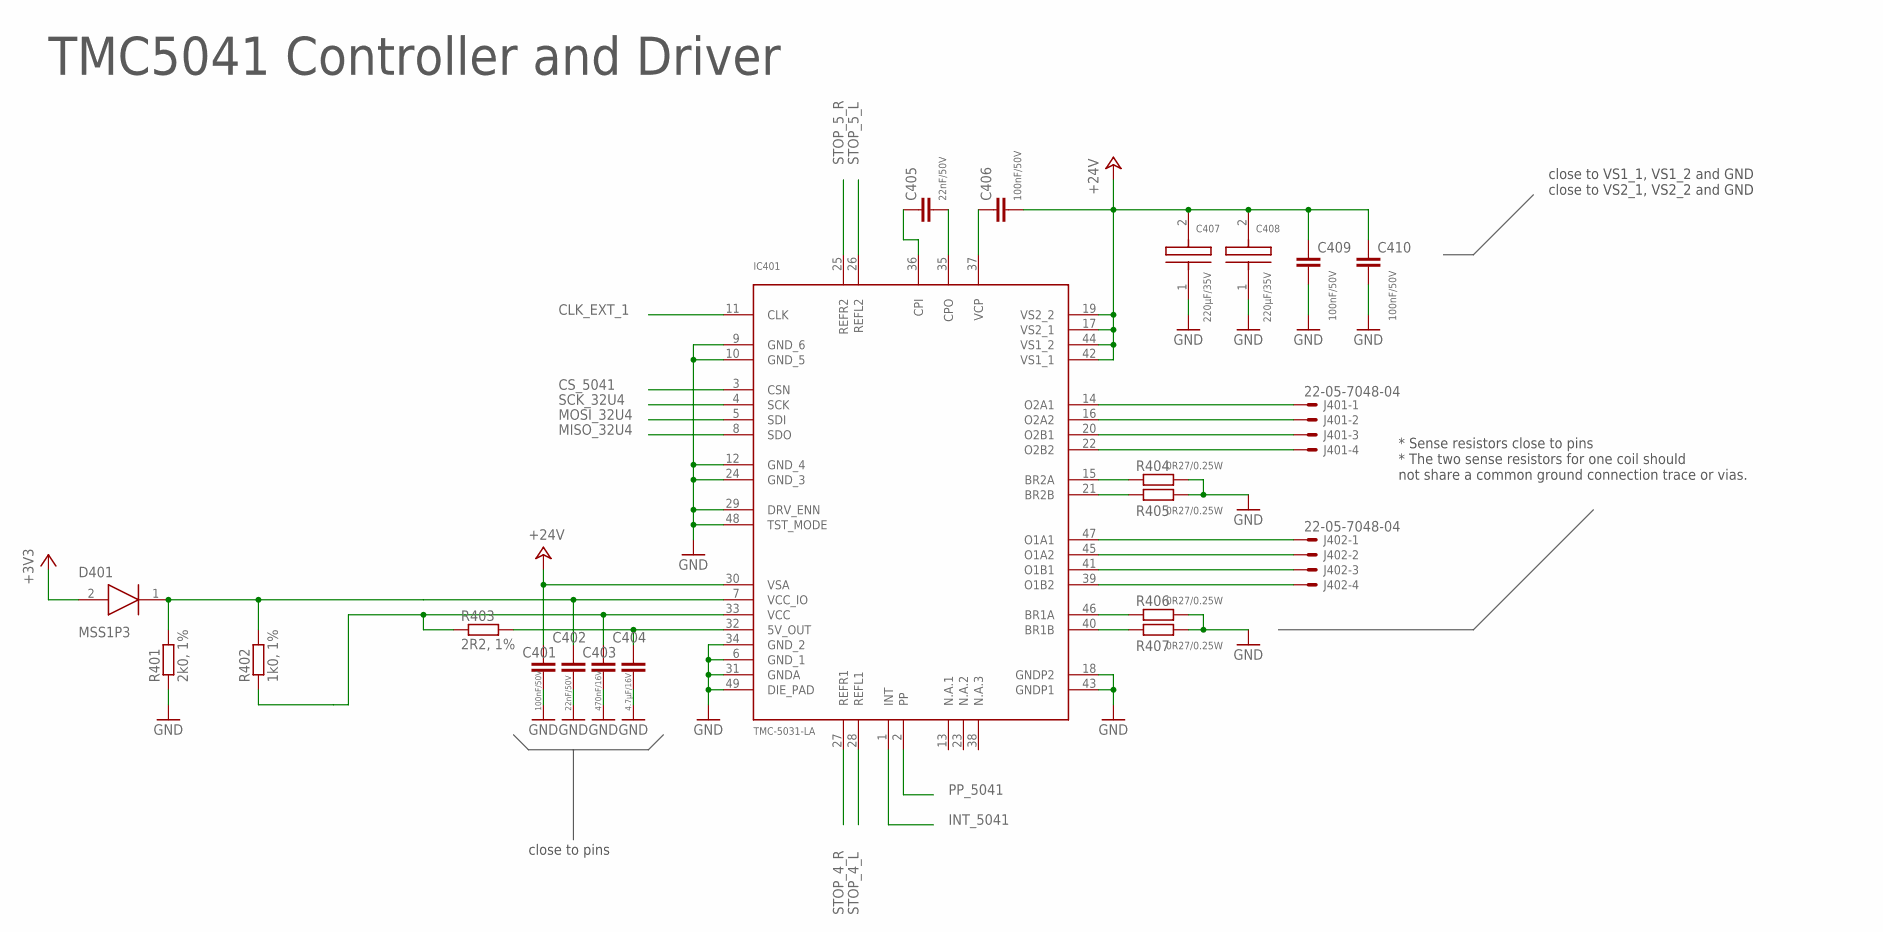
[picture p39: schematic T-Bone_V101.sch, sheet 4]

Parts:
C401, C406, C409, C410: 100nF/50V; C0603K
C402, C405: 22nF/50V; C0603K
C403: 470nF/16V; C0603K
C404: 4.7µF/16V; C0603K
C407, C408: 220µF/35V; F
D401: MSS1P3; MSS1PX
IC401: TMC-5031-LA; QFN48
J401, J402: 22-05-7048-04; 7395-04
R401: 2k0, 1%; R0603
R402: 1k0, 1%; R0603
R403: 2R2, 1%; R0603
R404, R405, R406, R407: 0R27/0.25W; R1206

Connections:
5031_O1A1: IC401.47 (O1A1), J402.1
5031_O1A2: IC401.45 (O1A2), J402.2
5031_O1B1: IC401.41 (O1B1), J402.3
5031_O1B2: IC401.39 (O1B2), J402.4
5031_O2A1: IC401.14 (O2A1), J401.1
5031_O2A2: IC401.16 (O2A2), J401.2
5031_O2B1: IC401.20 (O2B1), J401.3
5031_O2B2: IC401.22 (O2B2), J401.4
+3V3: D401.2 (ANODE); also elsewhere on the board
+24V: C401.1, C406.2, C407.2, C408.2, C409.1, C410.1, IC401.17 (VS2_1), IC401.19 (VS2_2), IC401.30 (VSA), IC401.42 (VS1_1), IC401.44 (VS1_2); also elsewhere on the board
CLK_EXT_1: IC401.11 (CLK); also elsewhere on the board
CS_5041: IC401.3 (CSN); also elsewhere on the board
GND: C401.2, C402.2, C403.2, C404.2, C407.1, C408.1, C409.2, C410.2, IC401.6 (GND_1), IC401.9 (GND_6), IC401.10 (GND_5), IC401.12 (GND_4), IC401.18 (GNDP2), IC401.24 (GND_3), IC401.29 (DRV_ENN), IC401.31 (GNDA), IC401.34 (GND_2), IC401.43 (GNDP1), IC401.48 (TST_MODE), IC401.49 (DIE_PAD), R401.1, R404.2, R405.2, R406.2, R407.2; also elsewhere on the board
INT_5041: IC401.1 (INT); also elsewhere on the board
MISO_32U4: IC401.8 (SDO); also elsewhere on the board
MOSI_32U4: IC401.5 (SDI); also elsewhere on the board
unnamed: C403.1, IC401.33 (VCC), R402.1, R403.1
unnamed: C405.2, IC401.35 (CPO)
unnamed: C405.1, IC401.36 (CPI)
unnamed: C406.1, IC401.37 (VCP)
unnamed: C404.1, IC401.32 (5V_OUT), R403.2
unnamed: IC401.21 (BR2B), R405.1
unnamed: IC401.15 (BR2A), R404.1
unnamed: IC401.40 (BR1B), R407.1
unnamed: IC401.46 (BR1A), R406.1
unnamed: C402.1, D401.1 (KATHODE), IC401.7 (VCC_IO), R401.2, R402.2
PP_5041: IC401.2 (PP); also elsewhere on the board
SCK_32U4: IC401.4 (SCK); also elsewhere on the board
STOP_4_L: IC401.28 (REFL1); also elsewhere on the board
STOP_4_R: IC401.27 (REFR1); also elsewhere on the board
STOP_5_L: IC401.26 (REFL2); also elsewhere on the board
STOP_5_R: IC401.25 (REFR2); also elsewhere on the board

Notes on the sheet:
TMC5041 Controller and Driver
close to VS1_1, VS1_2 and GND close to VS2_1, VS2_2 and GND
close to pins
* Sense resistors close to pins * The two sense resistors for one coil should not share a common ground connection trace or vias.

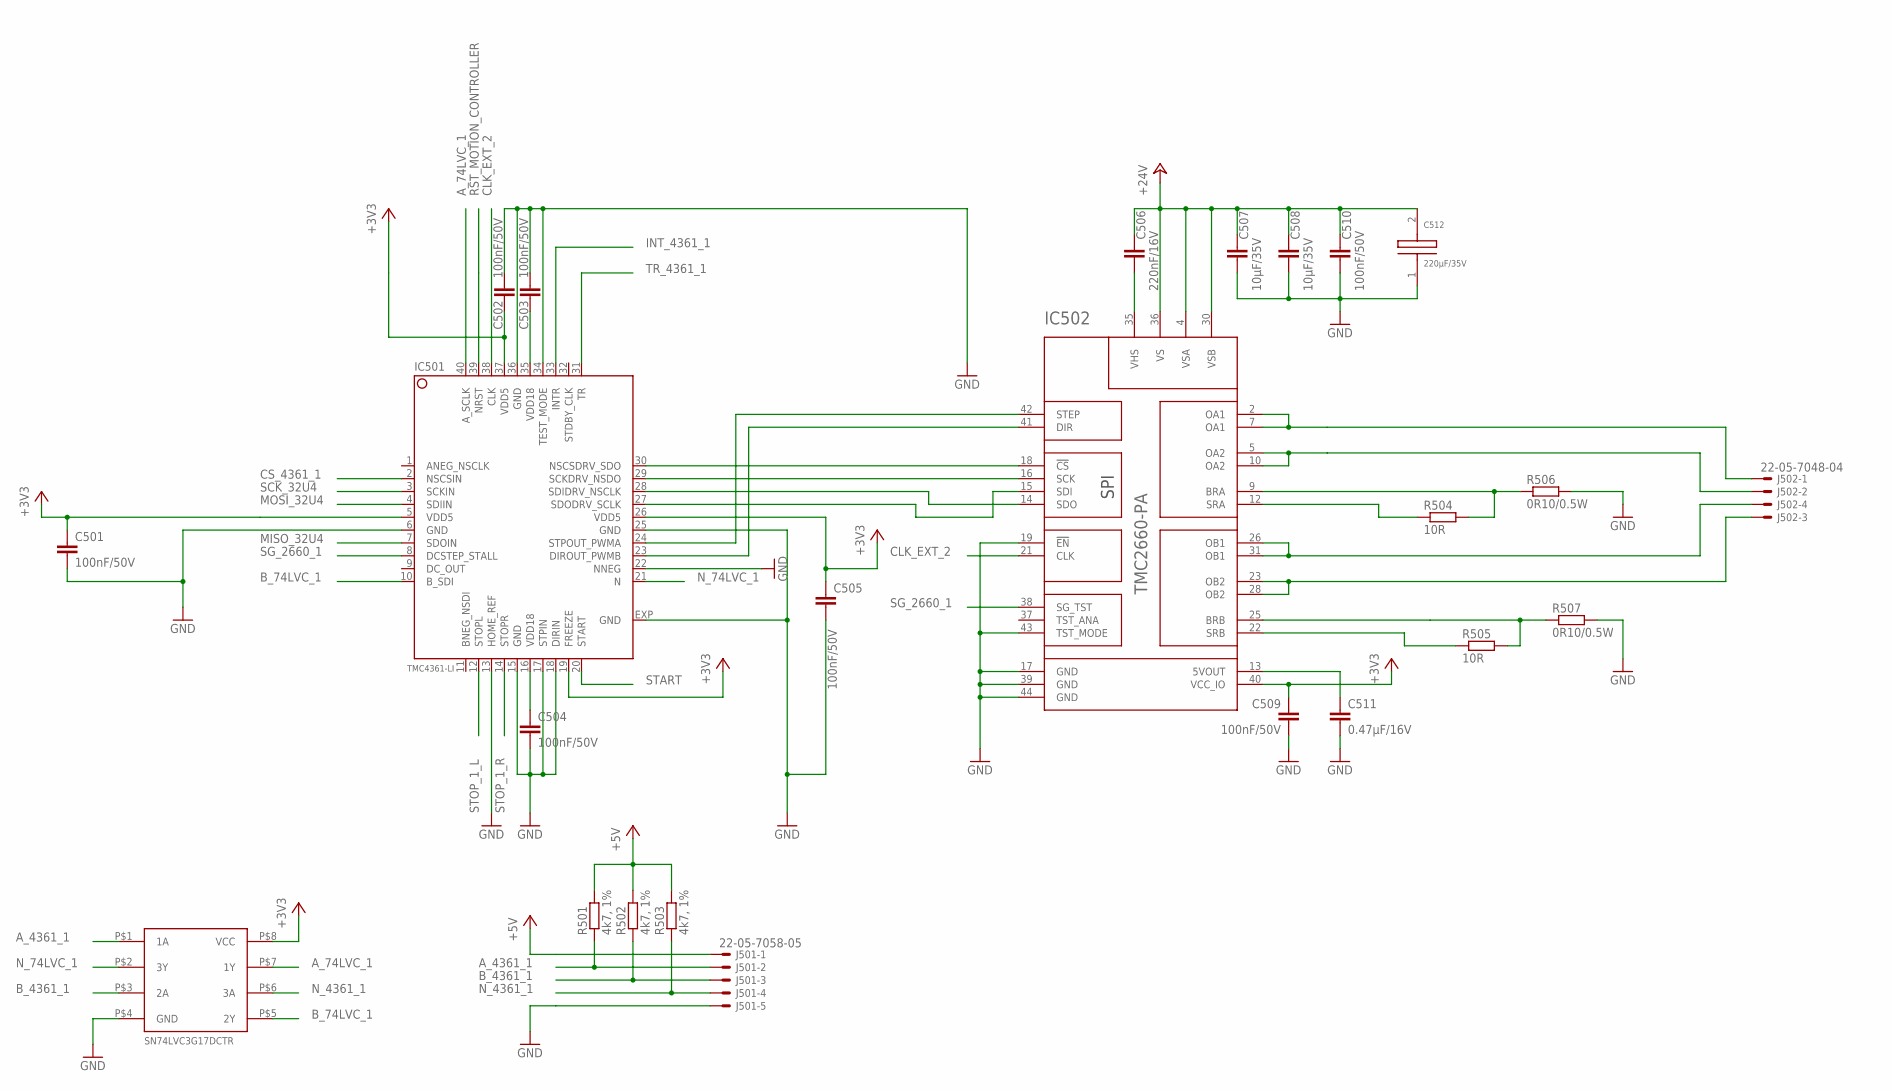
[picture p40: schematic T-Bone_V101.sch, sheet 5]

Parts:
C501, C502, C503, C504, C505, C509, C510: 100nF/50V; C0603K
C506: 220nF/16V; C0603K
C507, C508: 10µF/35V; C1210K
C511: 0.47µF/16V; C0603K
C512: 220µF/35V; F
IC501: TMC4361-LI; QFN40L
IC502: TMC2660-PA; PQFP44_WITH_PADS
J501: 22-05-7058-05; 7395-05
J502: 22-05-7048-04; 7395-04
R501, R502, R503: 4k7, 1%; R0603
R504, R505: 10R; R0603
R506, R507: 0R10/0.5W; R1206
U$501: SN74LVC3G17-SM8

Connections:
+3V3: C501.1, C502.2, C505.1, C509.1, IC501.5 (VDD5), IC501.19 (FREEZE), IC501.26 (VDD5), IC501.37 (VDD5), IC502.40 (VCC_IO), U$501.P$8 (VCC); also elsewhere on the board
+5V: J501.1, R501.2, R502.2, R503.2; also elsewhere on the board
+24V: C506.1, C507.1, C508.1, C510.1, C512.2, IC502.4 (VSA), IC502.30 (VSB), IC502.36 (VS); also elsewhere on the board
A_74LVC_1: IC501.40 (A_SCLK), U$501.P$7 (1Y)
A_4361_1: J501.2, R501.1, U$501.P$1 (1A)
B_74LVC_1: IC501.10 (B_SDI), U$501.P$5 (2Y)
B_4361_1: J501.3, R502.1, U$501.P$3 (2A)
CLK_EXT_2: IC501.38 (CLK), IC502.21 (CLK); also elsewhere on the board
CS_4361_1: IC501.2 (NSCSIN); also elsewhere on the board
GND: C501.2, C502.1, C503.1, C504.2, C505.2, C507.2, C508.2, C509.2, C510.2, C511.2, C512.1, IC501.6 (GND), IC501.13 (HOME_REF), IC501.15 (GND), IC501.17 (STPIN), IC501.18 (DIRIN), IC501.22 (NNEG), IC501.25 (GND), IC501.34 (TEST_MODE), IC501.36 (GND), IC501.EXP (GND), IC502.17 (GND), IC502.19 (!EN), IC502.39 (GND), IC502.43 (TST_MODE), IC502.44 (GND), J501.5, R506.2, R507.2, U$501.P$4 (GND); also elsewhere on the board
IC502_OA1: IC502.2 (OA1), IC502.7 (OA1), J502.1
IC502_OA2: IC502.5 (OA2), IC502.10 (OA2), J502.2
IC502_OB1: IC502.26 (OB1), IC502.31 (OB1), J502.4
IC502_OB2: IC502.23 (OB2), IC502.28 (OB2), J502.3
INT_4361_1: IC501.33 (INTR); also elsewhere on the board
MISO_32U4: IC501.7 (SDOIN); also elsewhere on the board
MOSI_32U4: IC501.4 (SDIIN); also elsewhere on the board
unnamed: IC501.28 (SDIDRV_NSCLK), IC502.14 (SDO)
unnamed: IC501.27 (SDODRV_SCLK), IC502.15 (SDI)
unnamed: IC501.29 (SCKDRV_NSDO), IC502.16 (SCK)
unnamed: IC501.30 (NSCSDRV_SDO), IC502.18 (!CS)
unnamed: C511.1, IC502.13 (5VOUT)
unnamed: C506.2, IC502.35 (VHS)
unnamed: IC502.22 (SRB), R505.1
unnamed: IC502.25 (BRB), R505.2, R507.1
unnamed: IC502.12 (SRA), R504.1
unnamed: IC502.9 (BRA), R504.2, R506.1
unnamed: IC501.24 (STPOUT_PWMA), IC502.42 (STEP)
unnamed: IC501.23 (DIROUT_PWMB), IC502.41 (DIR)
unnamed: C503.2, IC501.35 (VDD18)
unnamed: C504.1, IC501.16 (VDD18)
N_74LVC_1: IC501.21 (N), U$501.P$2 (3Y)
N_4361_1: J501.4, R503.1, U$501.P$6 (3A)
RST_MOTION_CONTROLLER: IC501.39 (NRST); also elsewhere on the board
SCK_32U4: IC501.3 (SCKIN); also elsewhere on the board
SG_2660_1: IC501.8 (DCSTEP_STALL), IC502.38 (SG_TST)
START: IC501.20 (START); also elsewhere on the board
STOP_1_L: IC501.12 (STOPL); also elsewhere on the board
STOP_1_R: IC501.14 (STOPR); also elsewhere on the board
TR_4361_1: IC501.31 (TR); also elsewhere on the board

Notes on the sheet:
SN74LVC3G17DCTR

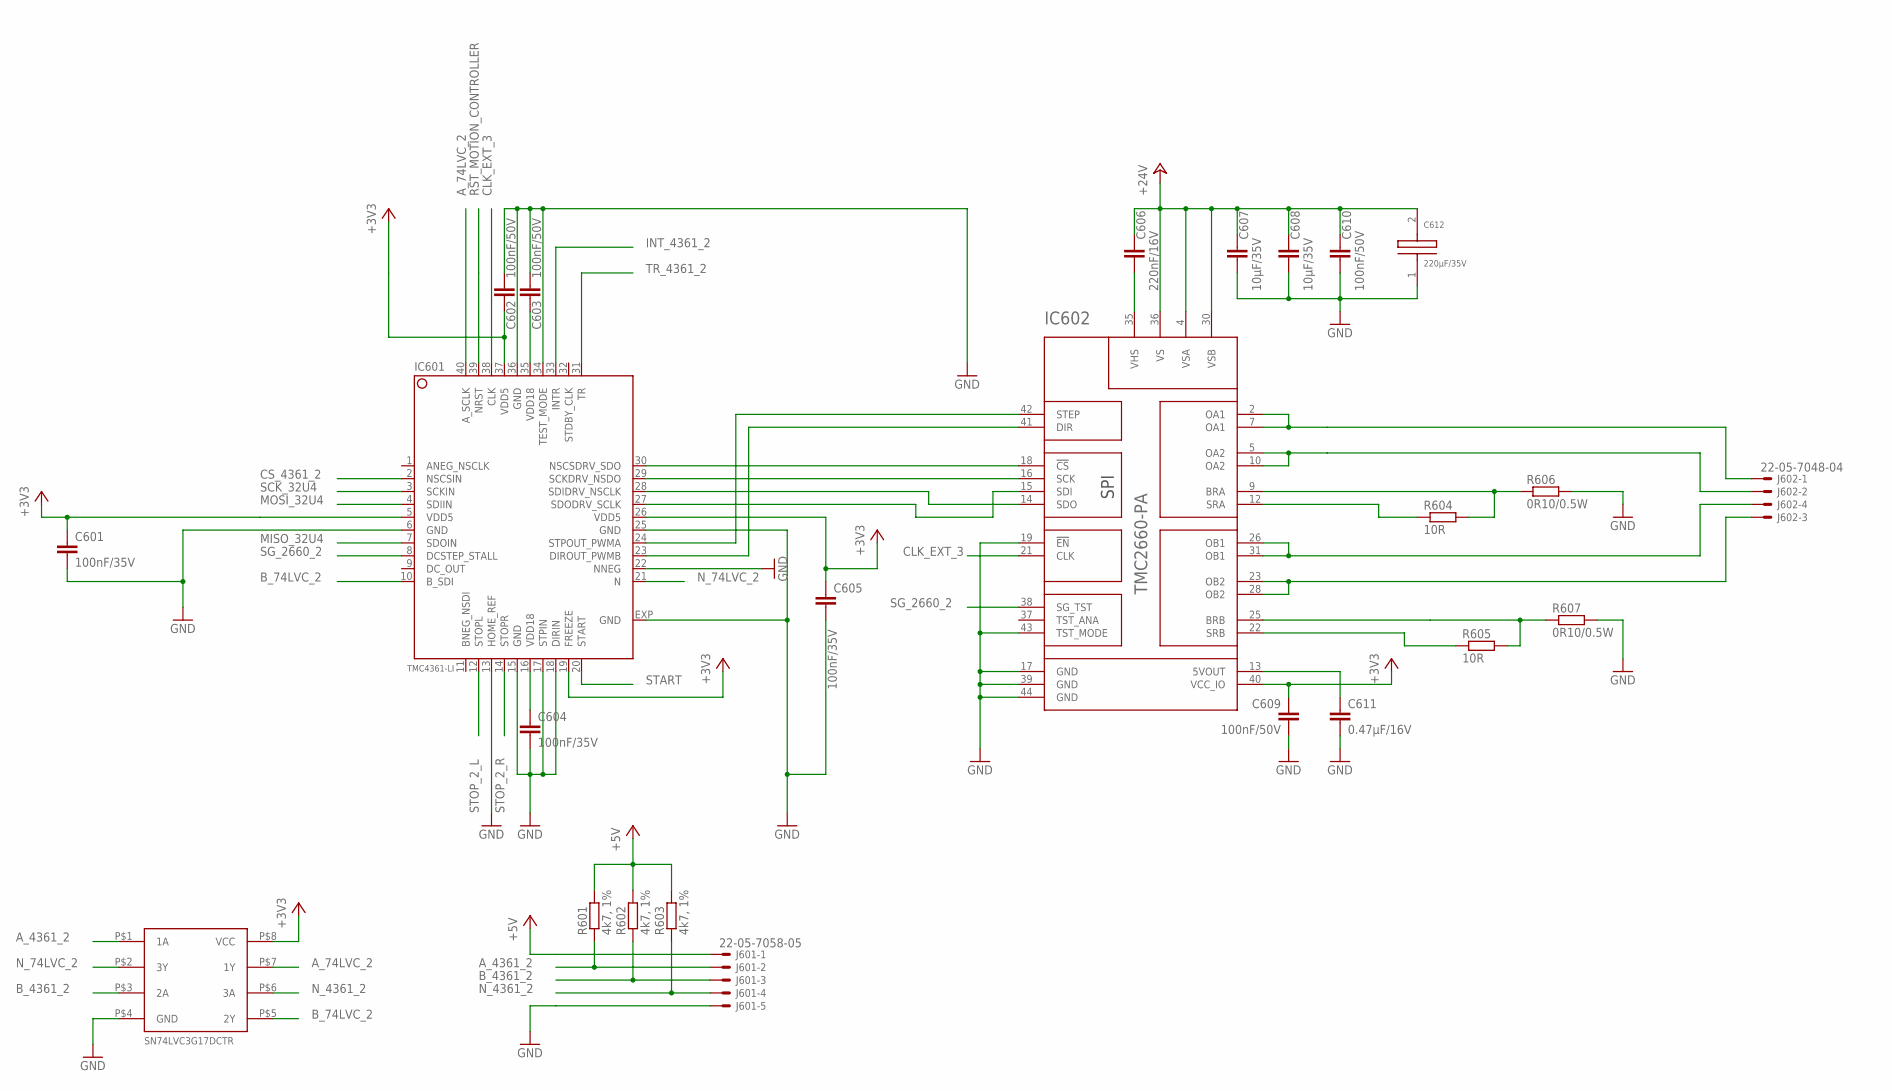
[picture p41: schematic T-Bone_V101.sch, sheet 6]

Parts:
C601, C604, C605: 100nF/35V; C0603K
C602, C603, C609, C610: 100nF/50V; C0603K
C606: 220nF/16V; C0603K
C607, C608: 10µF/35V; C1210K
C611: 0.47µF/16V; C0603K
C612: 220µF/35V; F
IC601: TMC4361-LI; QFN40L
IC602: TMC2660-PA; PQFP44_WITH_PADS
J601: 22-05-7058-05; 7395-05
J602: 22-05-7048-04; 7395-04
R601, R602, R603: 4k7, 1%; R0603
R604, R605: 10R; R0603
R606, R607: 0R10/0.5W; R1206
U$601: SN74LVC3G17-SM8

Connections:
+3V3: C601.1, C602.2, C605.1, C609.1, IC601.5 (VDD5), IC601.19 (FREEZE), IC601.26 (VDD5), IC601.37 (VDD5), IC602.40 (VCC_IO), U$601.P$8 (VCC); also elsewhere on the board
+5V: J601.1, R601.2, R602.2, R603.2; also elsewhere on the board
+24V: C606.1, C607.1, C608.1, C610.1, C612.2, IC602.4 (VSA), IC602.30 (VSB), IC602.36 (VS); also elsewhere on the board
A_74LVC_2: IC601.40 (A_SCLK), U$601.P$7 (1Y)
A_4361_2: J601.2, R601.1, U$601.P$1 (1A)
B_74LVC_2: IC601.10 (B_SDI), U$601.P$5 (2Y)
B_4361_2: J601.3, R602.1, U$601.P$3 (2A)
CLK_EXT_3: IC601.38 (CLK), IC602.21 (CLK); also elsewhere on the board
CS_4361_2: IC601.2 (NSCSIN); also elsewhere on the board
GND: C601.2, C602.1, C603.1, C604.2, C605.2, C607.2, C608.2, C609.2, C610.2, C611.2, C612.1, IC601.6 (GND), IC601.13 (HOME_REF), IC601.15 (GND), IC601.17 (STPIN), IC601.18 (DIRIN), IC601.22 (NNEG), IC601.25 (GND), IC601.34 (TEST_MODE), IC601.36 (GND), IC601.EXP (GND), IC602.17 (GND), IC602.19 (!EN), IC602.39 (GND), IC602.43 (TST_MODE), IC602.44 (GND), J601.5, R606.2, R607.2, U$601.P$4 (GND); also elsewhere on the board
IC602_OA1: IC602.2 (OA1), IC602.7 (OA1), J602.1
IC602_OA2: IC602.5 (OA2), IC602.10 (OA2), J602.2
IC602_OB1: IC602.26 (OB1), IC602.31 (OB1), J602.4
IC602_OB2: IC602.23 (OB2), IC602.28 (OB2), J602.3
INT_4361_2: IC601.33 (INTR); also elsewhere on the board
MISO_32U4: IC601.7 (SDOIN); also elsewhere on the board
MOSI_32U4: IC601.4 (SDIIN); also elsewhere on the board
unnamed: IC601.28 (SDIDRV_NSCLK), IC602.14 (SDO)
unnamed: IC601.27 (SDODRV_SCLK), IC602.15 (SDI)
unnamed: IC601.29 (SCKDRV_NSDO), IC602.16 (SCK)
unnamed: IC602.9 (BRA), R604.2, R606.1
unnamed: IC602.12 (SRA), R604.1
unnamed: IC601.30 (NSCSDRV_SDO), IC602.18 (!CS)
unnamed: C606.2, IC602.35 (VHS)
unnamed: IC601.24 (STPOUT_PWMA), IC602.42 (STEP)
unnamed: IC601.23 (DIROUT_PWMB), IC602.41 (DIR)
unnamed: C611.1, IC602.13 (5VOUT)
unnamed: IC602.25 (BRB), R605.2, R607.1
unnamed: IC602.22 (SRB), R605.1
unnamed: C603.2, IC601.35 (VDD18)
unnamed: C604.1, IC601.16 (VDD18)
N_74LVC_2: IC601.21 (N), U$601.P$2 (3Y)
N_4361_2: J601.4, R603.1, U$601.P$6 (3A)
RST_MOTION_CONTROLLER: IC601.39 (NRST); also elsewhere on the board
SCK_32U4: IC601.3 (SCKIN); also elsewhere on the board
SG_2660_2: IC601.8 (DCSTEP_STALL), IC602.38 (SG_TST)
START: IC601.20 (START); also elsewhere on the board
STOP_2_L: IC601.12 (STOPL); also elsewhere on the board
STOP_2_R: IC601.14 (STOPR); also elsewhere on the board
TR_4361_2: IC601.31 (TR); also elsewhere on the board

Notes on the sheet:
SN74LVC3G17DCTR

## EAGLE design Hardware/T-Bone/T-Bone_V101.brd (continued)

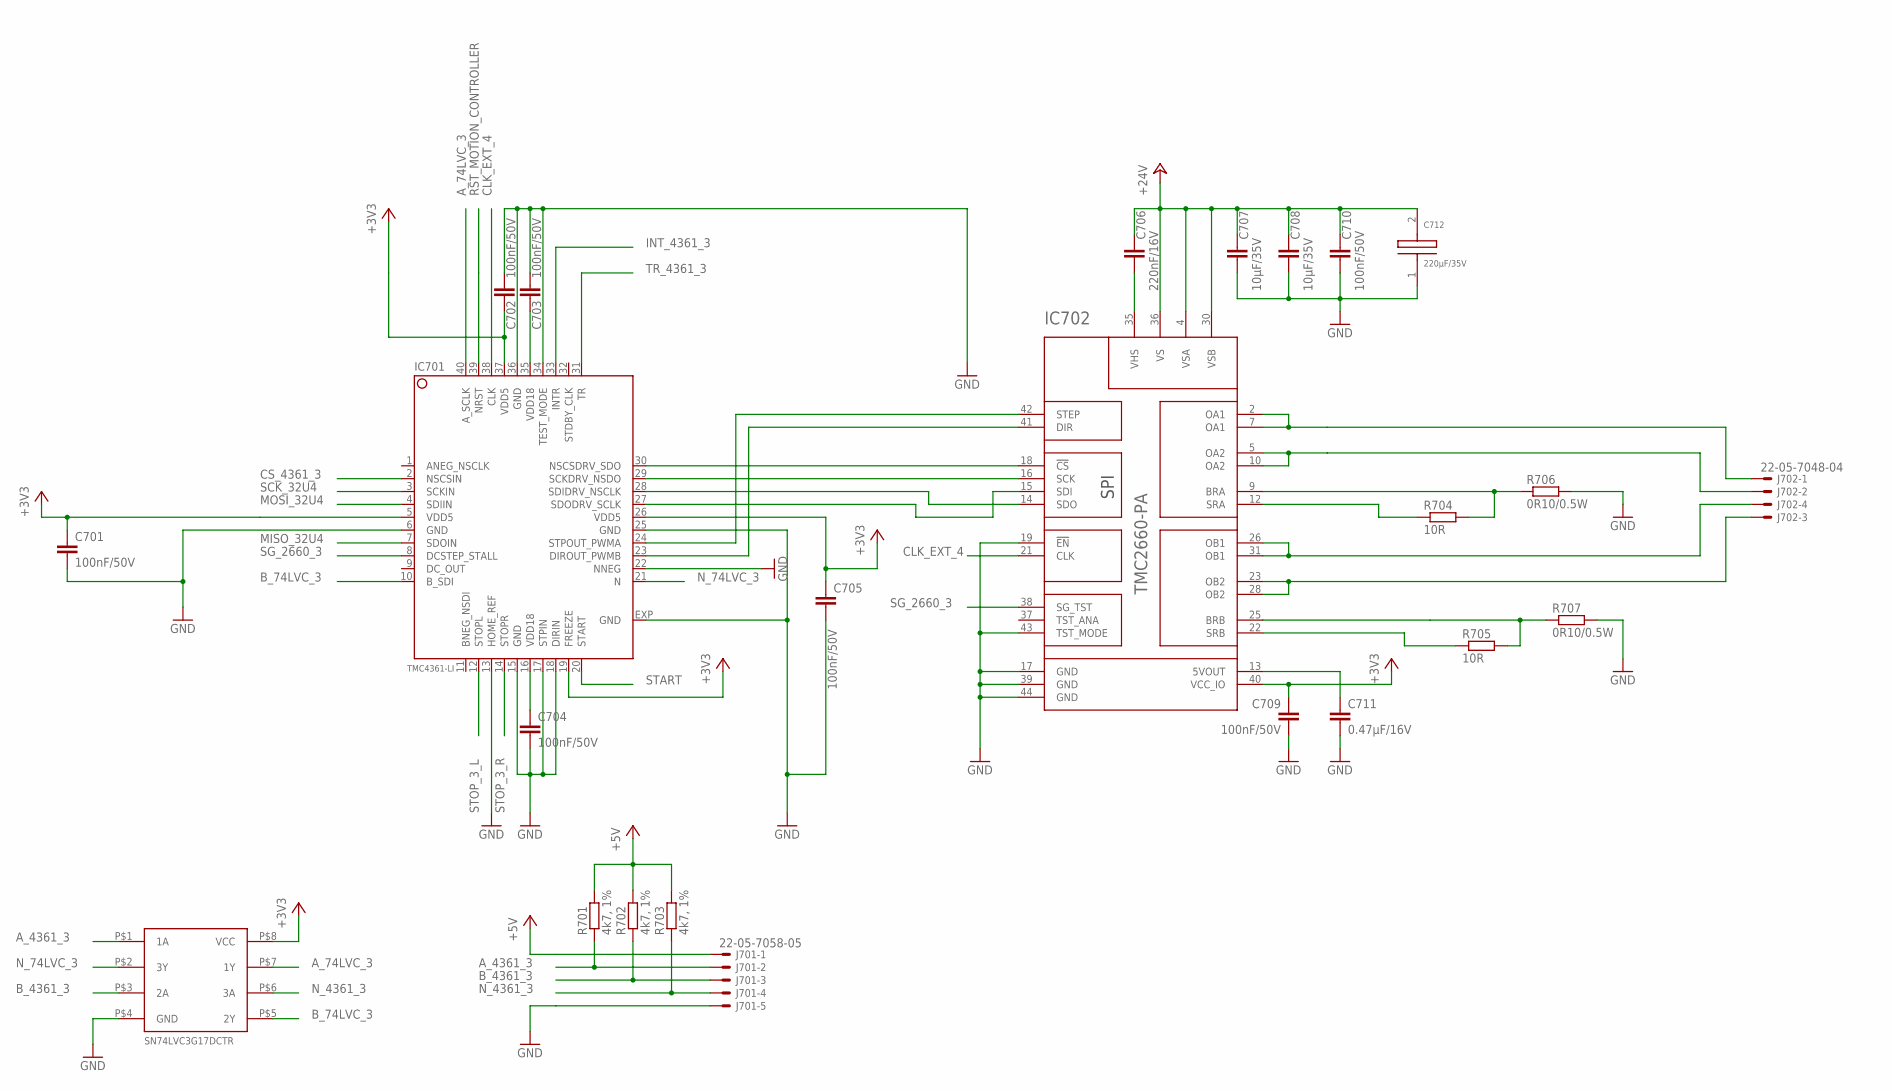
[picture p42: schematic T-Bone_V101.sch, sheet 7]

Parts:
C701, C702, C703, C704, C705, C709, C710: 100nF/50V; C0603K
C706: 220nF/16V; C0603K
C707, C708: 10µF/35V; C1210K
C711: 0.47µF/16V; C0603K
C712: 220µF/35V; F
IC701: TMC4361-LI; QFN40L
IC702: TMC2660-PA; PQFP44_WITH_PADS
J701: 22-05-7058-05; 7395-05
J702: 22-05-7048-04; 7395-04
R701, R702, R703: 4k7, 1%; R0603
R704, R705: 10R; R0603
R706, R707: 0R10/0.5W; R1206
U$701: SN74LVC3G17-SM8

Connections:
+3V3: C701.1, C702.2, C705.1, C709.1, IC701.5 (VDD5), IC701.19 (FREEZE), IC701.26 (VDD5), IC701.37 (VDD5), IC702.40 (VCC_IO), U$701.P$8 (VCC); also elsewhere on the board
+5V: J701.1, R701.2, R702.2, R703.2; also elsewhere on the board
+24V: C706.1, C707.1, C708.1, C710.1, C712.2, IC702.4 (VSA), IC702.30 (VSB), IC702.36 (VS); also elsewhere on the board
A_74LVC_3: IC701.40 (A_SCLK), U$701.P$7 (1Y)
A_4361_3: J701.2, R701.1, U$701.P$1 (1A)
B_74LVC_3: IC701.10 (B_SDI), U$701.P$5 (2Y)
B_4361_3: J701.3, R702.1, U$701.P$3 (2A)
CLK_EXT_4: IC701.38 (CLK), IC702.21 (CLK); also elsewhere on the board
CS_4361_3: IC701.2 (NSCSIN); also elsewhere on the board
GND: C701.2, C702.1, C703.1, C704.2, C705.2, C707.2, C708.2, C709.2, C710.2, C711.2, C712.1, IC701.6 (GND), IC701.13 (HOME_REF), IC701.15 (GND), IC701.17 (STPIN), IC701.18 (DIRIN), IC701.22 (NNEG), IC701.25 (GND), IC701.34 (TEST_MODE), IC701.36 (GND), IC701.EXP (GND), IC702.17 (GND), IC702.19 (!EN), IC702.39 (GND), IC702.43 (TST_MODE), IC702.44 (GND), J701.5, R706.2, R707.2, U$701.P$4 (GND); also elsewhere on the board
IC702_OA1: IC702.2 (OA1), IC702.7 (OA1), J702.1
IC702_OA2: IC702.5 (OA2), IC702.10 (OA2), J702.2
IC702_OB1: IC702.26 (OB1), IC702.31 (OB1), J702.4
IC702_OB2: IC702.23 (OB2), IC702.28 (OB2), J702.3
INT_4361_3: IC701.33 (INTR); also elsewhere on the board
MISO_32U4: IC701.7 (SDOIN); also elsewhere on the board
MOSI_32U4: IC701.4 (SDIIN); also elsewhere on the board
unnamed: IC701.24 (STPOUT_PWMA), IC702.42 (STEP)
unnamed: IC701.23 (DIROUT_PWMB), IC702.41 (DIR)
unnamed: IC701.28 (SDIDRV_NSCLK), IC702.14 (SDO)
unnamed: IC701.27 (SDODRV_SCLK), IC702.15 (SDI)
unnamed: C711.1, IC702.13 (5VOUT)
unnamed: IC702.9 (BRA), R704.2, R706.1
unnamed: IC702.12 (SRA), R704.1
unnamed: IC701.29 (SCKDRV_NSDO), IC702.16 (SCK)
unnamed: IC701.30 (NSCSDRV_SDO), IC702.18 (!CS)
unnamed: C706.2, IC702.35 (VHS)
unnamed: IC702.25 (BRB), R705.2, R707.1
unnamed: IC702.22 (SRB), R705.1
unnamed: C703.2, IC701.35 (VDD18)
unnamed: C704.1, IC701.16 (VDD18)
N_74LVC_3: IC701.21 (N), U$701.P$2 (3Y)
N_4361_3: J701.4, R703.1, U$701.P$6 (3A)
RST_MOTION_CONTROLLER: IC701.39 (NRST); also elsewhere on the board
SCK_32U4: IC701.3 (SCKIN); also elsewhere on the board
SG_2660_3: IC701.8 (DCSTEP_STALL), IC702.38 (SG_TST)
START: IC701.20 (START); also elsewhere on the board
STOP_3_L: IC701.12 (STOPL); also elsewhere on the board
STOP_3_R: IC701.14 (STOPR); also elsewhere on the board
TR_4361_3: IC701.31 (TR); also elsewhere on the board

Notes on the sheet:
SN74LVC3G17DCTR

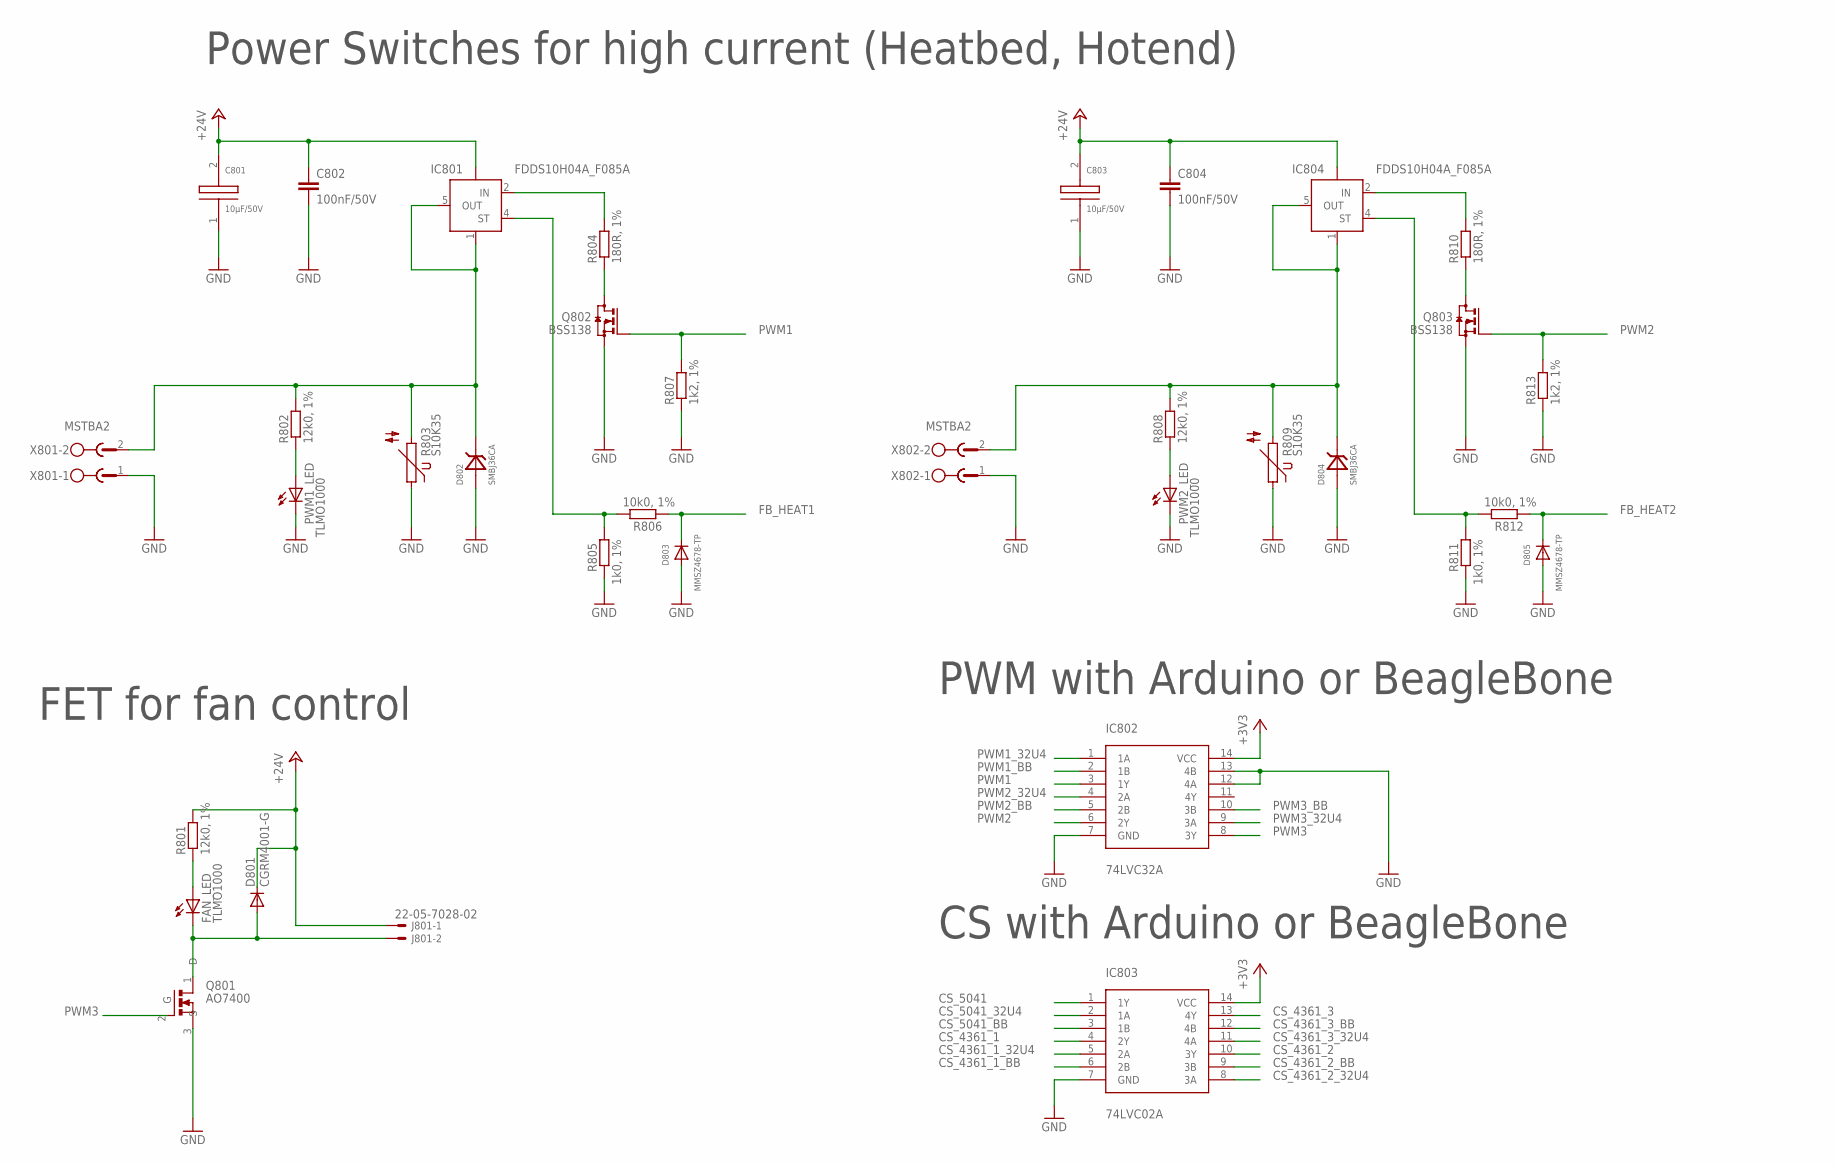
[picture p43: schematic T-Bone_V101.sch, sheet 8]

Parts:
C801, C803: 10µF/50V; D8
C802, C804: 100nF/50V; C0805K
D801: CGRM4001-G; SOD-123_MINI-SMA
D802, D804: SMBJ36CA; SMB
D803, D805: MMSZ4678-TP; SOD-123
FAN_LED: TLMO1000; CHIP-LED0603
IC801, IC804: FDDS10H04A_F085A; TO252-5-11
IC802: 74LVC32A; 14-VFQFN
IC803: 74LVC02A; 14-VFQFN
J801: 22-05-7028-02; 7395-02
PWM1_LED, PWM2_LED: TLMO1000; CHIP-LED0603
Q801: AO7400; SOT323
Q802, Q803: BSS138; SOT23
R801, R802, R808: 12k0, 1%; R0603
R803, R809: S10K35; S10K40
R804, R810: 180R, 1%; R0603
R805, R811: 1k0, 1%; R0603
R806, R812: 10k0, 1%; R0603
R807, R813: 1k2, 1%; R0603
X801, X802: MSTBA2

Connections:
+3V3: IC802.14 (VCC), IC803.14 (VCC); also elsewhere on the board
+24V: C801.2, C802.1, C803.2, C804.1, D801.C, IC801.TAB (VBB), IC804.TAB (VBB), J801.1, R801.2; also elsewhere on the board
CS_4361_1: IC803.4 (2Y); also elsewhere on the board
CS_4361_1_32U4: IC803.5 (2A); also elsewhere on the board
CS_4361_1_BB: IC803.6 (2B); also elsewhere on the board
CS_4361_2: IC803.10 (3Y); also elsewhere on the board
CS_4361_2_32U4: IC803.8 (3A); also elsewhere on the board
CS_4361_2_BB: IC803.9 (3B); also elsewhere on the board
CS_4361_3: IC803.13 (4Y); also elsewhere on the board
CS_4361_3_32U4: IC803.11 (4A); also elsewhere on the board
CS_4361_3_BB: IC803.12 (4B); also elsewhere on the board
CS_5041: IC803.1 (1Y); also elsewhere on the board
CS_5041_32U4: IC803.2 (1A); also elsewhere on the board
CS_5041_BB: IC803.3 (1B); also elsewhere on the board
FB_HEAT1: D803.C, R806.1; also elsewhere on the board
FB_HEAT2: D805.C, R812.1; also elsewhere on the board
GND: C801.1, C802.2, C803.1, C804.2, D802.A, D803.A, D804.A, D805.A, IC802.7 (GND), IC802.12 (4A), IC802.13 (4B), IC803.7 (GND), PWM1_LED.C, PWM2_LED.C, Q801.3 (S), Q802.2 (S), Q803.2 (S), R803.1, R805.1, R807.1, R809.1, R811.1, R813.1, X801.1, X802.1; also elsewhere on the board
HEAT1: D802.C, IC801.1 (GND), IC801.5 (OUT), R802.2, R803.2, X801.2
HEAT2: D804.C, IC804.1 (GND), IC804.5 (OUT), R808.2, R809.2, X802.2
unnamed: Q802.3 (D), R804.1
unnamed: D801.A, FAN_LED.C, J801.2, Q801.1 (D)
unnamed: FAN_LED.A, R801.1
unnamed: PWM1_LED.A, R802.1
unnamed: PWM2_LED.A, R808.1
unnamed: IC801.4 (ST), R805.2, R806.2
unnamed: IC801.2 (IN), R804.2
unnamed: Q803.3 (D), R810.1
unnamed: IC804.4 (ST), R811.2, R812.2
unnamed: IC804.2 (IN), R810.2
PWM1: IC802.3 (1Y), Q802.1 (G), R807.2
PWM1_32U4: IC802.1 (1A); also elsewhere on the board
PWM1_BB: IC802.2 (1B); also elsewhere on the board
PWM2: IC802.6 (2Y), Q803.1 (G), R813.2
PWM2_32U4: IC802.4 (2A); also elsewhere on the board
PWM2_BB: IC802.5 (2B); also elsewhere on the board
PWM3: IC802.8 (3Y), Q801.2 (G)
PWM3_32U4: IC802.9 (3A); also elsewhere on the board
PWM3_BB: IC802.10 (3B); also elsewhere on the board

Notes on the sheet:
CS with Arduino or BeagleBone
PWM with Arduino or BeagleBone
FET for fan control
Power Switches for high current (Heatbed, Hotend)

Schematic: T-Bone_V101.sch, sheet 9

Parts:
END1L_LED, END1R_LED, END2L_LED, END2R_LED, END3L_LED, END3R_LED, END4L_LED, END4R_LED, END5L_LED, END5R_LED: LEDCHIP-LED0603; CHIP-LED0603
J450, J460, J470, J480, J550, J560, J650, J660, J750, J760: 22-05-7038-03; 7395-03
R450, R451, R460, R461, R470, R471, R480, R481, R550, R551, R560, R561, R650, R651, R660, R661, R750, R751, R760, R761: 4k7, 1%; R0402
R452, R462, R472, R482, R552, R562, R652, R662, R752, R762: 10k; R0402
SJ450, SJ460, SJ470, SJ480, SJ550, SJ560, SJ650, SJ660, SJ750, SJ760: SJ2W; SJ_2

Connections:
+3V3: J450.1, J460.1, J470.1, J480.1, J550.1, J560.1, J650.1, J660.1, J750.1, J760.1, R451.2, R461.2, R471.2, R481.2, R551.2, R561.2, R651.2, R661.2, R751.2, R761.2; also elsewhere on the board
GND: J450.3, J460.3, J470.3, J480.3, J550.3, J560.3, J650.3, J660.3, J750.3, J760.3, R450.1, R452.1, R460.1, R462.1, R470.1, R472.1, R480.1, R482.1, R550.1, R552.1, R560.1, R562.1, R650.1, R652.1, R660.1, R662.1, R750.1, R752.1, R760.1, R762.1; also elsewhere on the board
unnamed: R471.1, SJ470.1
unnamed: END1L_LED.C, R552.2
unnamed: END2L_LED.C, R652.2
unnamed: R470.2, SJ470.3
unnamed: END4L_LED.C, R452.2
unnamed: END3L_LED.C, R752.2
unnamed: END1R_LED.C, R562.2
unnamed: END2R_LED.C, R662.2
unnamed: END4R_LED.C, R462.2
unnamed: END3R_LED.C, R762.2
unnamed: END5L_LED.C, R472.2
unnamed: R481.1, SJ480.1
unnamed: R480.2, SJ480.3
unnamed: END5R_LED.C, R482.2
unnamed: R650.2, SJ650.3
unnamed: R651.1, SJ650.1
unnamed: R451.1, SJ450.1
unnamed: R550.2, SJ550.3
unnamed: R551.1, SJ550.1
unnamed: R450.2, SJ450.3
unnamed: R560.2, SJ560.3
unnamed: R561.1, SJ560.1
unnamed: R661.1, SJ660.1
unnamed: R660.2, SJ660.3
unnamed: R460.2, SJ460.3
unnamed: R461.1, SJ460.1
unnamed: R751.1, SJ750.1
unnamed: R750.2, SJ750.3
unnamed: R761.1, SJ760.1
unnamed: R760.2, SJ760.3
STOP_1_L: END1L_LED.A, J550.2, SJ550.2; also elsewhere on the board
STOP_1_R: END1R_LED.A, J560.2, SJ560.2; also elsewhere on the board
STOP_2_L: END2L_LED.A, J650.2, SJ650.2; also elsewhere on the board
STOP_2_R: END2R_LED.A, J660.2, SJ660.2; also elsewhere on the board
STOP_3_L: END3L_LED.A, J750.2, SJ750.2; also elsewhere on the board
STOP_3_R: END3R_LED.A, J760.2, SJ760.2; also elsewhere on the board
STOP_4_L: END4L_LED.A, J450.2, SJ450.2; also elsewhere on the board
STOP_4_R: END4R_LED.A, J460.2, SJ460.2; also elsewhere on the board
STOP_5_L: END5L_LED.A, J470.2, SJ470.2; also elsewhere on the board
STOP_5_R: END5R_LED.A, J480.2, SJ480.2; also elsewhere on the board

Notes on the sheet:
Connectors for Endstops (Pullup/-down optional)

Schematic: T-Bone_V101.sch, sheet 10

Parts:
C901, C902, C903, C904, C905, C906: 470nF/50V; C0402K
J902, J904, J907: 22-05-7028-02; 7395-02
R901, R903, R905: 4k7, 1%; R0402
R902, R904, R906: 6k8, 1%; R0402

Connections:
1V8_ADC_BB: R901.2, R903.2, R905.2; also elsewhere on the board
GND: C901.2, C902.2, C903.2, C904.2, C905.2, C906.2, J902.2, J904.2, J907.2; also elsewhere on the board
unnamed: C901.1, J902.1, R901.1, R902.1
unnamed: C903.1, J904.1, R903.1, R904.1
unnamed: C905.1, J907.1, R905.1, R906.1
TEMP1: C902.1, R902.2; also elsewhere on the board
TEMP2: C904.1, R904.2; also elsewhere on the board
TEMP3: C906.1, R906.2; also elsewhere on the board

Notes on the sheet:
Connectors for Thermistors

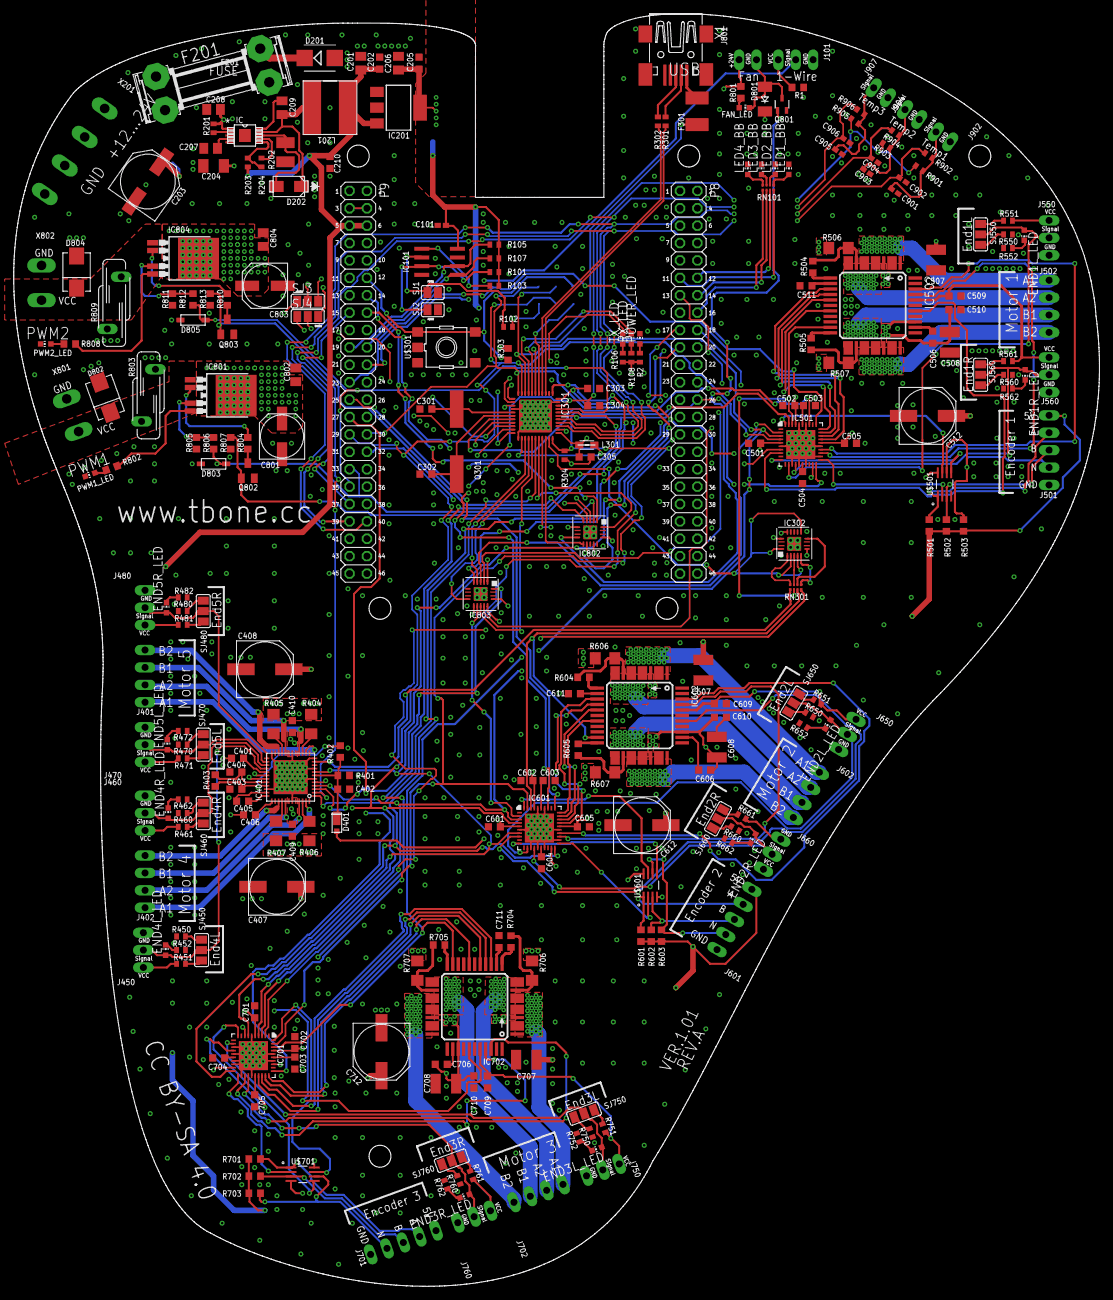
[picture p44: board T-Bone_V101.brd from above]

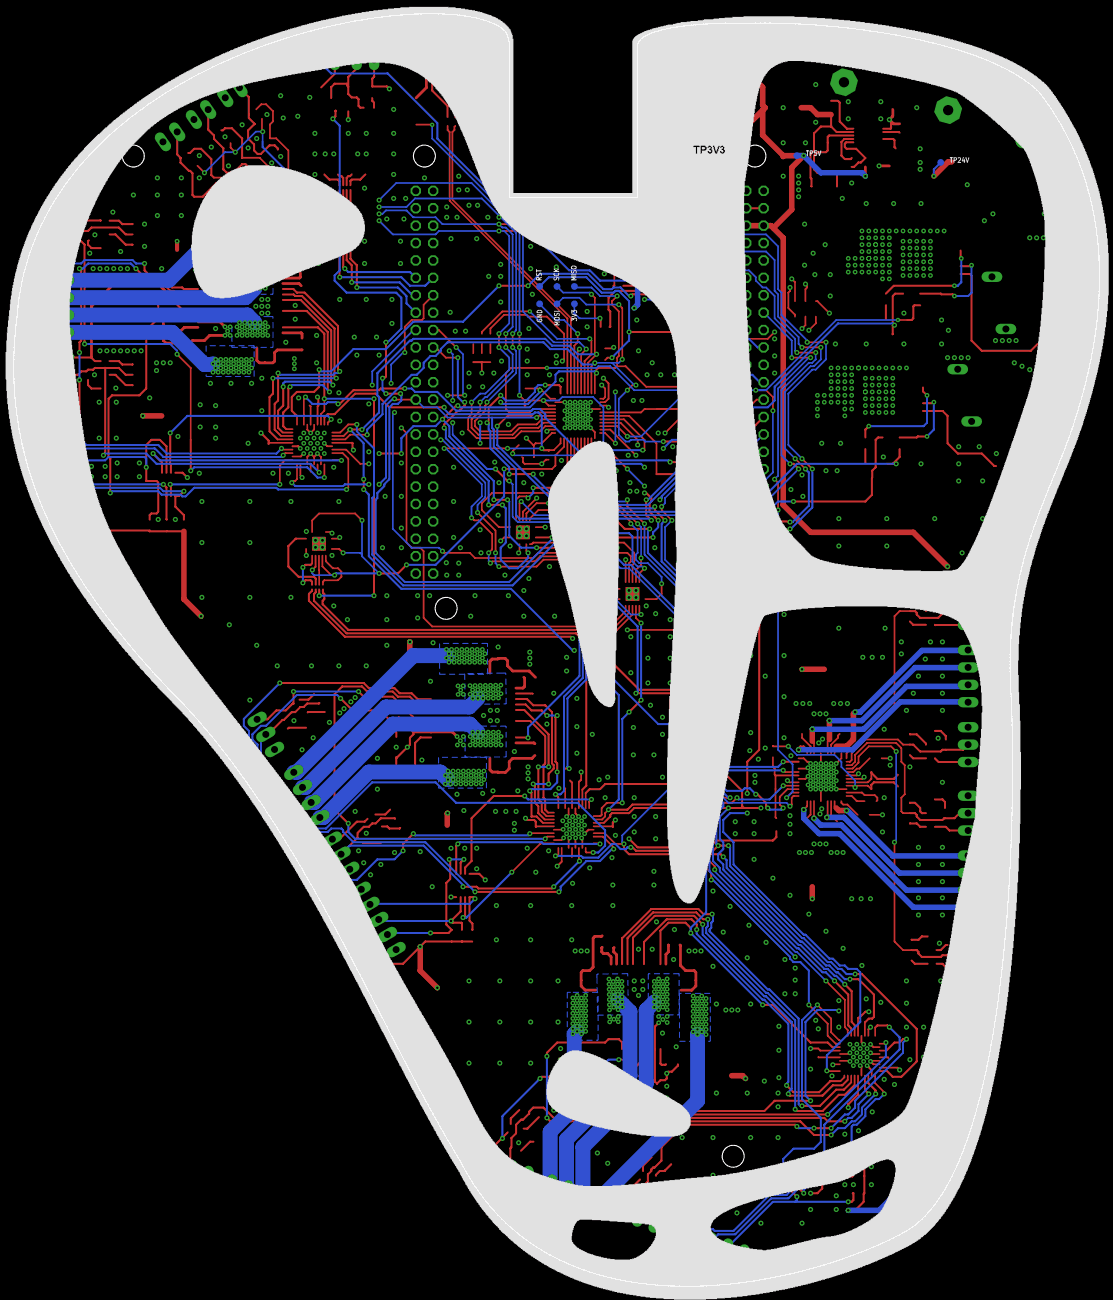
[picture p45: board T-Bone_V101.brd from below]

Board: 4 copper layers, 158.5 x 185.8 mm, 277 parts (9 on the bottom side), 244 nets.

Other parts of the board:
U$1: T-BONE_SILK_EXT_WITH_3V3

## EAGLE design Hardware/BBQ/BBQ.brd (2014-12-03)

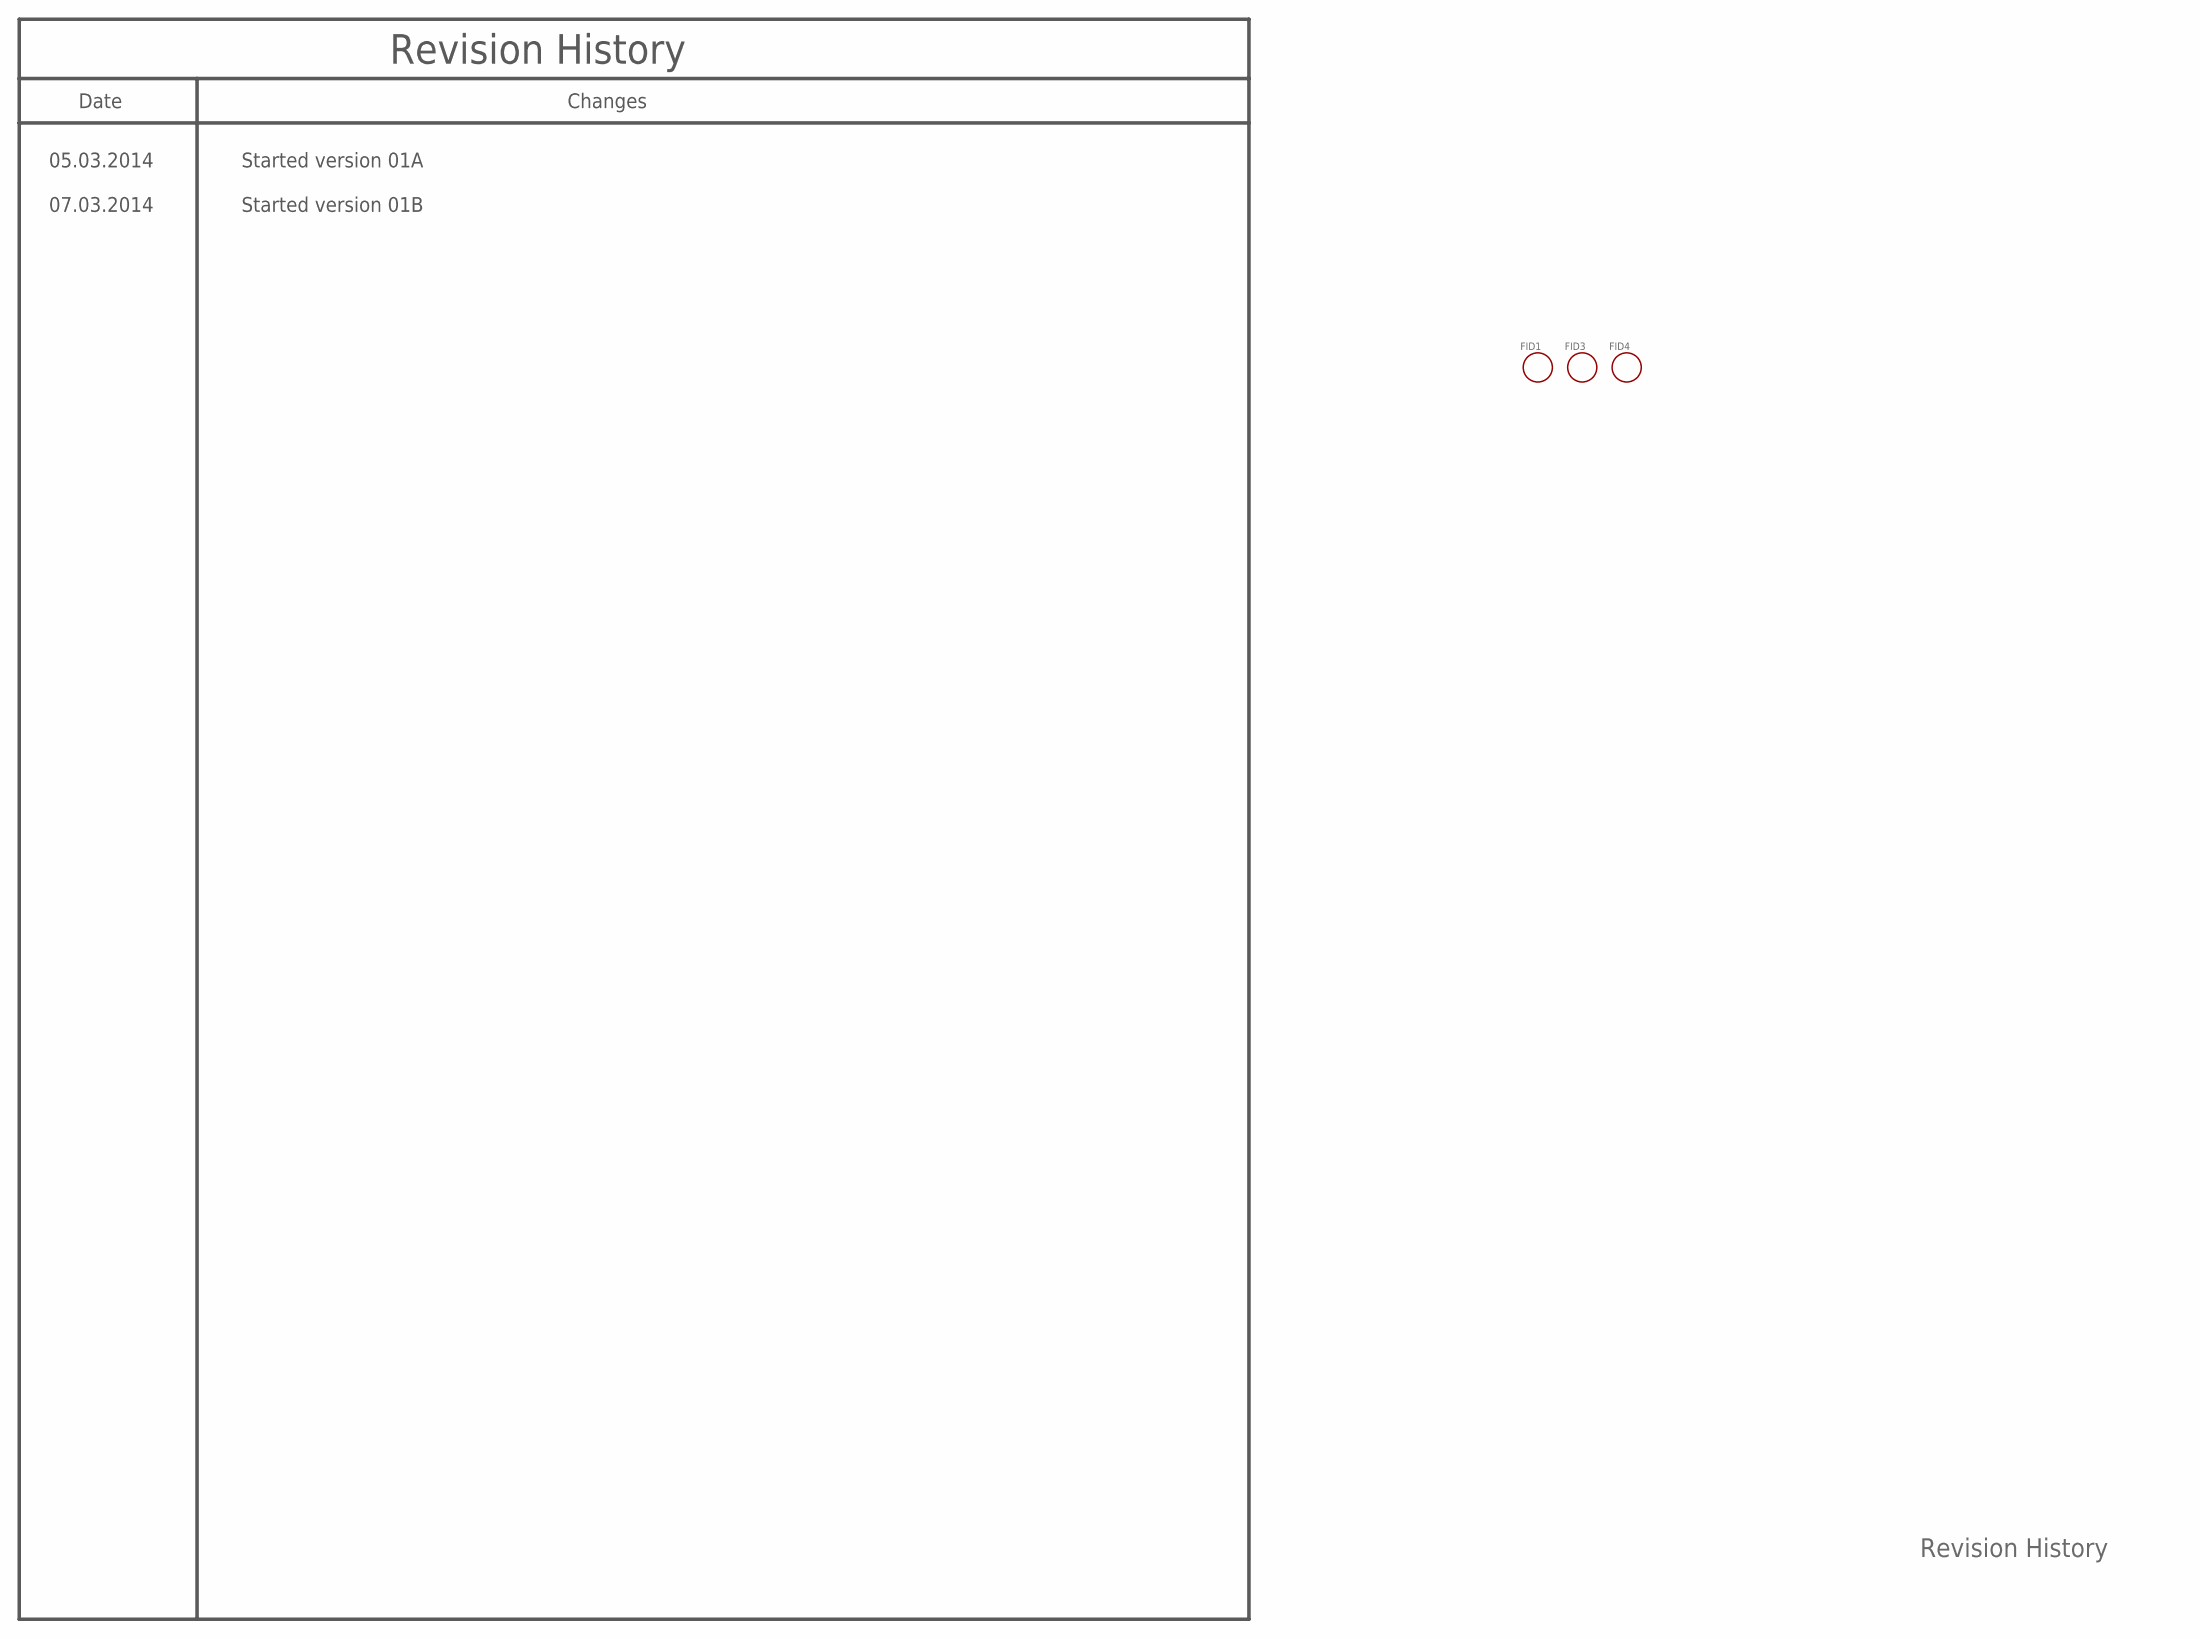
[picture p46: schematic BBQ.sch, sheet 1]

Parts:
FID1, FID3, FID4: FIDUCIAL

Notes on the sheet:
Revision History
Changes
Date
05.03.2014
Started version 01A
07.03.2014
Started version 01B

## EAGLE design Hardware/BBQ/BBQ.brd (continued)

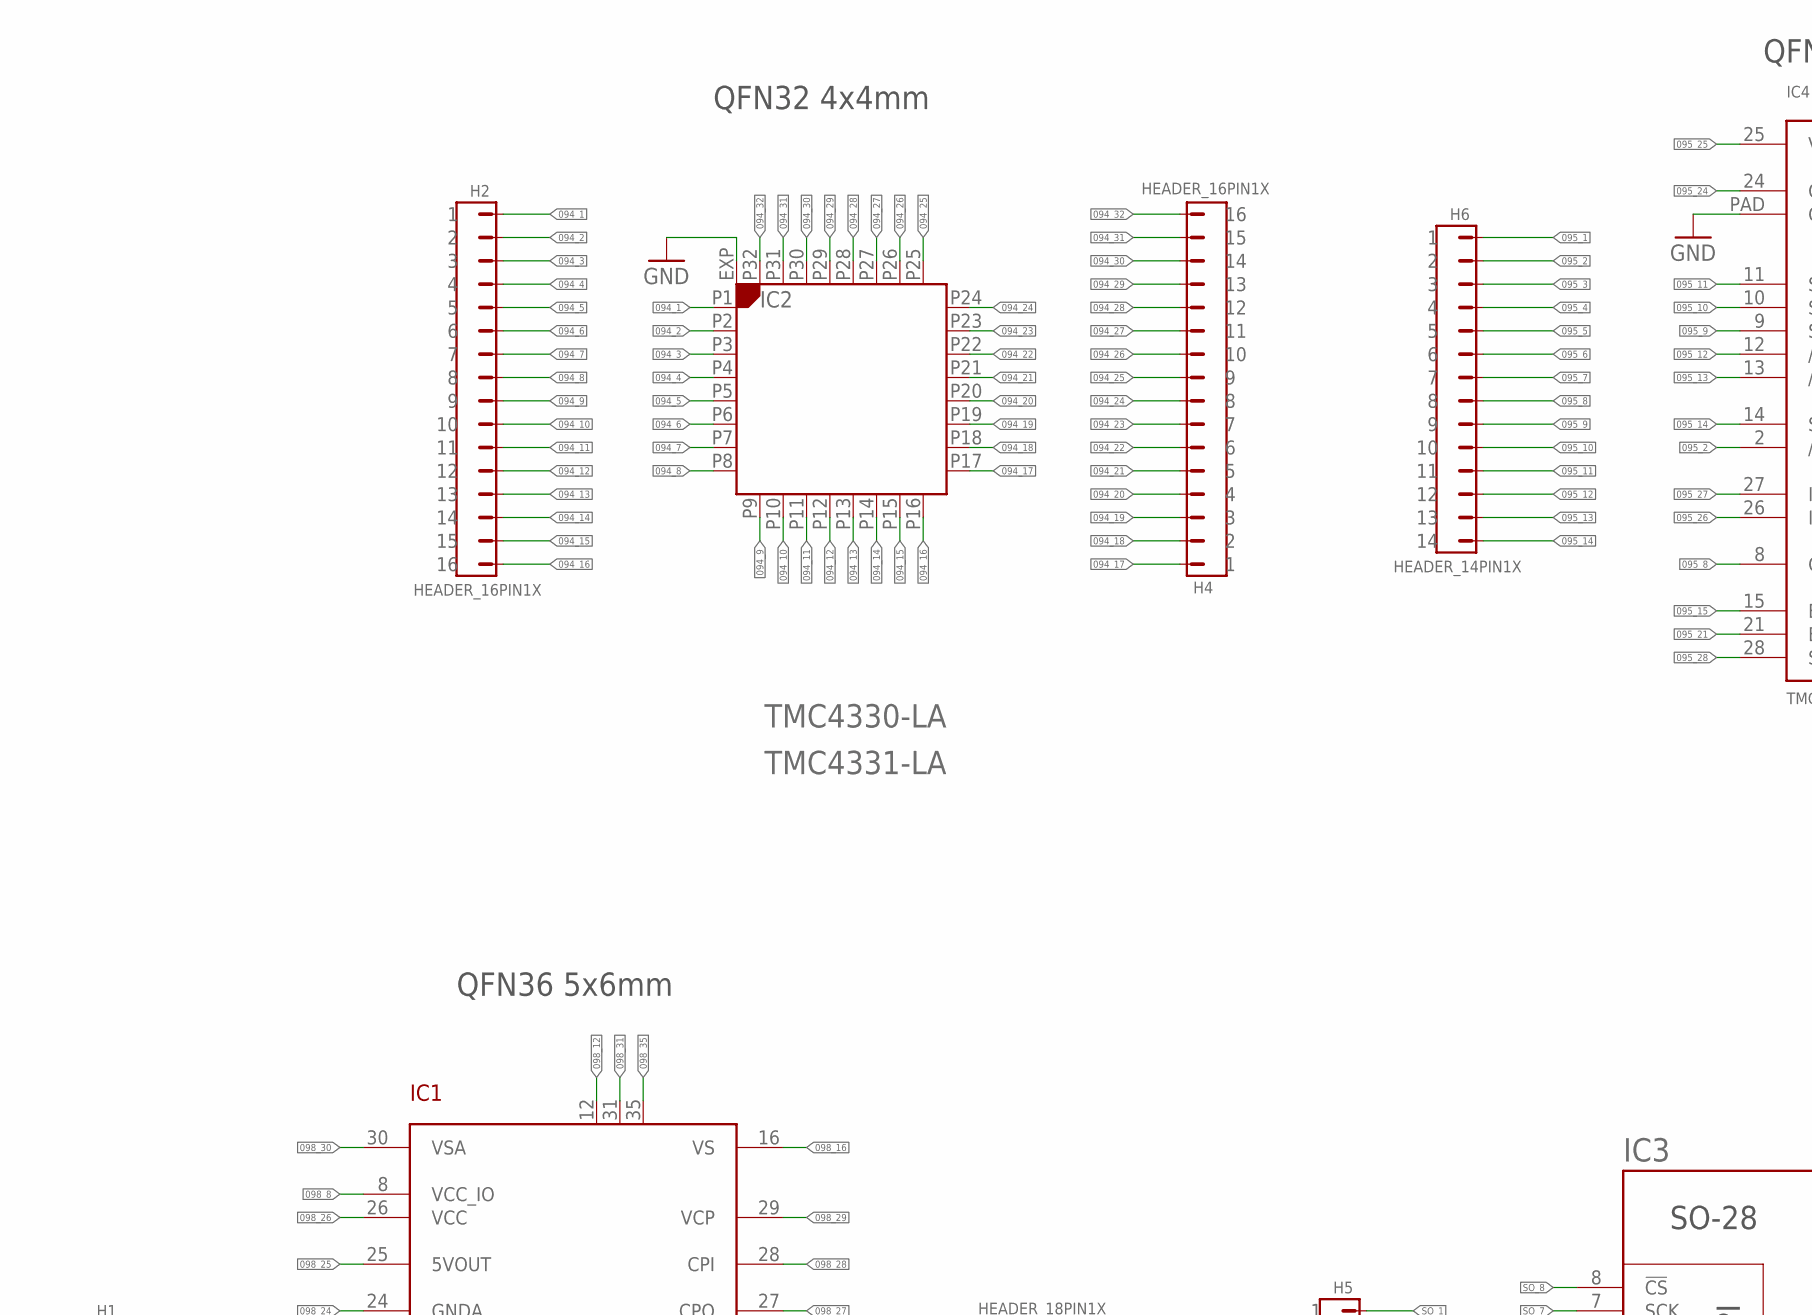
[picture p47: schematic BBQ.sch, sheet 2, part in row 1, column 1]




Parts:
H1, H3: HEADER_18PIN1X; 18PIN_2.54_TH
H2, H4: HEADER_16PIN1X; 16PIN_2.54_TH
H5, H6, H7, H8: HEADER_14PIN1X; 14PIN_2.54_TH
H9, H11, H12, H13: HEADER_10PIN1X; 10PIN_2.54_TH
H10, H14: HEADER_8PIN1X; 8PIN_2.54_TH
IC1: TMC2130_QFN36; QFN36
IC2: TMC4330-LA; QFN-32_4X4
IC3: TMC249A-SA; SO28
IC4: TMC248; QFN28_5X5
IC5: TMC4361; QFN40L
IC6: TMC429-I; SSOP16

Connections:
094_1: H2.1, IC2.P1
094_2: H2.2, IC2.P2
094_3: H2.3, IC2.P3
094_4: H2.4, IC2.P4
094_5: H2.5, IC2.P5
094_6: H2.6, IC2.P6
094_7: H2.7, IC2.P7
094_8: H2.8, IC2.P8
094_9: H2.9, IC2.P9
094_10: H2.10, IC2.P10
094_11: H2.11, IC2.P11
094_12: H2.12, IC2.P12
094_13: H2.13, IC2.P13
094_14: H2.14, IC2.P14
094_15: H2.15, IC2.P15
094_16: H2.16, IC2.P16
094_17: H4.1, IC2.P17
094_18: H4.2, IC2.P18
094_19: H4.3, IC2.P19
094_20: H4.4, IC2.P20
094_21: H4.5, IC2.P21
094_22: H4.6, IC2.P22
094_23: H4.7, IC2.P23
094_24: H4.8, IC2.P24
094_25: H4.9, IC2.P25
094_26: H4.10, IC2.P26
094_27: H4.11, IC2.P27
094_28: H4.12, IC2.P28
094_29: H4.13, IC2.P29
094_30: H4.14, IC2.P30
094_31: H4.15, IC2.P31
094_32: H4.16, IC2.P32
094_GND: IC2.EXP
095_1: H6.1, IC4.1 (AGND)
095_2: H6.2, IC4.2 (/AN)
095_3: H6.3, IC4.3 (HA1)
095_4: H6.4, IC4.4 (HA2)
095_5: H6.5, IC4.5 (LA1)
095_6: H6.6, IC4.6 (LA2)
095_7: H6.7, IC4.7 (SRA)
095_8: H6.8, IC4.8 (OSC)
095_9: H6.9, IC4.9 (SDO)
095_10: H6.10, IC4.10 (SDI)
095_11: H6.11, IC4.11 (SCK)
095_12: H6.12, IC4.12 (/CS)
095_13: H6.13, IC4.13 (/EN)
095_14: H6.14, IC4.14 (SPE)
095_15: H7.1, IC4.15 (BL1)
095_16: H7.2, IC4.16 (SRB)
095_17: H7.3, IC4.17 (LB2)
095_18: H7.4, IC4.18 (LB1)
095_19: H7.5, IC4.19 (HB2)
095_20: H7.6, IC4.20 (HB1)
095_21: H7.7, IC4.21 (BL2)
095_22: H7.8, IC4.22 (VT)
095_23: H7.9, IC4.23 (VS)
095_24: H7.10, IC4.24 (GND)
095_25: H7.11, IC4.25 (VCC)
095_26: H7.12, IC4.26 (INB)
095_27: H7.13, IC4.27 (INA)
095_28: H7.14, IC4.28 (SLP)
095_GND: IC4.PAD (GND)
097_GND: IC5.EXP (GND)
098_1: H1.1, IC1.1 (CLK)
098_2: H1.2, IC1.2 (CSN_CFG3)
098_3: H1.3, IC1.3 (SCK_CFG2)
098_4: H1.4, IC1.4 (SDI_NAI_CFG1)
098_5: H1.5, IC1.5 (SDO_NAO_CFG0)
098_6: H1.6, IC1.6 (REFL_STEP)
098_7: H1.7, IC1.7 (REFR_DIR)
098_8: H1.8, IC1.8 (VCC_IO)
098_9: H1.9, IC1.9 (SD_MODE)
098_10: H1.10, IC1.10 (SPI_MODE)
098_11: H1.11, IC1.11 (GND)
098_12: H1.12, IC1.12
098_13: H1.13, IC1.13 (OB1)
098_14: H1.14, IC1.14 (BRB)
098_15: H1.15, IC1.15 (OB2)
098_16: H1.16, IC1.16 (VS)
098_17: H1.17, IC1.17 (ENCN_DCO)
098_18: H1.18, IC1.18 (ENCB_DCEN_CFG4)
098_19: H3.1, IC1.19 (ENCA_DCIN_CFG5)
098_20: H3.2, IC1.20 (SWN_DIAG0)
098_21: H3.3, IC1.21 (SWP_DIAG1)
098_22: H3.4, IC1.22 (DRV_ENN_CFG6)
098_23: H3.5, IC1.23 (AIN_IREF)
098_24: H3.6, IC1.24 (GNDA)
098_25: H3.7, IC1.25 (5VOUT)
098_26: H3.8, IC1.26 (VCC)
098_27: H3.9, IC1.27 (CPO)
098_28: H3.10, IC1.28 (CPI)
098_29: H3.11, IC1.29 (VCP)
098_30: H3.12, IC1.30 (VSA)
098_31: H3.13, IC1.31
098_32: H3.14, IC1.32 (OA2)
098_33: H3.15, IC1.33 (BRA)
098_34: H3.16, IC1.34 (OA1)
098_35: H3.17, IC1.35
098_36: H3.18, IC1.36 (TST_MODE)
098_GND: IC1.GND_PAD (PAD)
unnamed: H9.1, IC5.1 (ANEG_NSCLK)
unnamed: H9.2, IC5.2 (NSCSIN)
unnamed: H9.3, IC5.3 (SCKIN)
unnamed: H9.4, IC5.4 (SDIIN)
unnamed: H9.5, IC5.5 (VDD5)
unnamed: H9.6, IC5.6 (GND)
unnamed: H9.7, IC5.7 (SDOIN)
unnamed: H9.8, IC5.8 (DCSTEP_STALL)
unnamed: H9.9, IC5.9 (DC_OUT)
unnamed: H9.10, IC5.10 (B_SDI)
unnamed: H11.1, IC5.11 (BNEG_NSDI)
unnamed: H11.2, IC5.12 (STOPL)
unnamed: H11.3, IC5.13 (HOME_REF)
unnamed: H11.4, IC5.14 (STOPR)
unnamed: H11.5, IC5.15 (GND)
unnamed: H11.6, IC5.16 (VDD18)
unnamed: H11.7, IC5.17 (STPIN)
unnamed: H11.8, IC5.18 (DIRIN)
unnamed: H11.9, IC5.19 (NFREEZE)
unnamed: H11.10, IC5.20 (START)
unnamed: H13.1, IC5.21 (N)
unnamed: H13.2, IC5.22 (NNEG)
unnamed: H13.3, IC5.23 (DIROUT_PWMB)
unnamed: H13.4, IC5.24 (STPOUT_PWMA)
unnamed: H13.5, IC5.25 (GND)
unnamed: H13.6, IC5.26 (VDD5)
unnamed: H13.7, IC5.27 (SDODRV_SCLK)
unnamed: H13.8, IC5.28 (SDIDRV_NSCLK)
unnamed: H13.9, IC5.29 (SCKDRV_NSDO)
unnamed: H13.10, IC5.30 (NSCSDRV_SDO)
unnamed: H12.1, IC5.31 (TR)
unnamed: H12.2, IC5.32 (STDBY_CLK)
unnamed: H12.3, IC5.33 (INTR)
unnamed: H12.4, IC5.34 (TEST_MODE)
unnamed: H12.5, IC5.35 (VDD18)
unnamed: H12.6, IC5.36 (GND)
unnamed: H12.7, IC5.37 (VDD5)
unnamed: H12.8, IC5.38 (CLK)
unnamed: H12.9, IC5.39 (NRST)
unnamed: H12.10, IC5.40 (A_SCLK)
SO_1: H5.1, IC3.1 (LA1)
SO_2: H5.2, IC3.2 (LA2)
SO_3: H5.3, IC3.3 (SRA)
SO_4: H5.4, IC3.4 (OSC)
SO_5: H5.5, IC3.5 (SDO)
SO_6: H5.6, IC3.6 (SDI)
SO_7: H5.7, IC3.7 (SCK)
SO_8: H5.8, IC3.8 (!CS)
SO_9: H5.9, IC3.9 (!EN)
SO_10: H5.10, IC3.10 (SPE)
SO_11: H5.11, IC3.11 (BL1)
SO_12: H5.12, IC3.12 (SRB)
SO_13: H5.13, IC3.13 (LB2)
SO_14: H5.14, IC3.14 (LB1)
SO_15: H8.1, IC3.15 (HB2)
SO_16: H8.2, IC3.16 (HB1)
SO_17: H8.3, IC3.17 (BL2)
SO_18: H8.4, IC3.18 (VT)
SO_19: H8.5, IC3.19 (VS)
SO_20: H8.6, IC3.20 (GND)
SO_21: H8.7, IC3.21 (VCC)
SO_22: H8.8, IC3.22 (INB)
SO_23: H8.9, IC3.23 (INA)
SO_24: H8.10, IC3.24 (SLP)
SO_25: H8.11, IC3.25 (AGND)
SO_26: H8.12, IC3.26 (!AN)
SO_27: H8.13, IC3.27 (HA1)
SO_28: H8.14, IC3.28 (HA2)
SSOP_1: H10.1, IC6.1 (REF1)
SSOP_2: H10.2, IC6.2 (REF2)
SSOP_3: H10.3, IC6.3 (REF3)
SSOP_4: H10.4, IC6.4 (TEST)
SSOP_5: H10.5, IC6.5 (CLK)
SSOP_6: H10.6, IC6.6 (!SCS_C)
SSOP_7: H10.7, IC6.7 (SCK_C)
SSOP_8: H10.8, IC6.8 (SDI_C)
SSOP_9: H14.1, IC6.9 (!INT!_SDO_C)
SSOP_10: H14.2, IC6.10 (SDO_S_S1)
SSOP_11: H14.3, IC6.11 (SCK_S_D1)
SSOP_12: H14.4, IC6.12 (!SCS_S_S2)
SSOP_13: H14.5, IC6.13 (V5)
SSOP_14: H14.6, IC6.14 (V33)
SSOP_15: H14.7, IC6.15 (GND)
SSOP_16: H14.8, IC6.16 (SDI_S_D2)

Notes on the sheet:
Panel 1_1
TMC4210
SSOP-16
TMC239A-SA
SO-28
TMC4330-LA
QFN32 4x4mm
TMC4331-LA
TMC248-LI
QFN28 5x5mm
TMC4361-LA
QFN40 6x6mm
TMC2130-LA TMC2100-LA TMC5130-LA
QFN36 5x6mm

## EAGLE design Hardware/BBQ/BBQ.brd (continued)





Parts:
H15, H16, H17, H18: HEADER_16PIN1X; 16PIN_2.54_TH
H19, H24: HEADER_8PIN1X; 8PIN_2.54_TH
H20, H21, H22, H23, H25, H26, H27, H28: HEADER_12PIN1X; 12PIN_2.54_TH
IC7: TMC262-LA; QFN32_5X5
IC8: TMC222-LI; QFN32_7X7
IC9: TMC5031-LA; QFN-48_7X7
IC10: TMC429-I; SSOP16
IC11: TMC_RHINO; TQFP48-EP

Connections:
092_1: H16.1, IC7.1 (GND)
092_2: H16.2, IC7.2 (HA1)
092_3: H16.3, IC7.3 (HA2)
092_4: H16.4, IC7.4 (BMA2)
092_5: H16.5, IC7.5 (BMA1)
092_6: H16.6, IC7.6 (LA1)
092_7: H16.7, IC7.7 (LA2)
092_8: H16.8, IC7.8 (SRA)
092_9: H16.9, IC7.9 (5VOUT)
092_10: H16.10, IC7.10 (SDO)
092_11: H16.11, IC7.11 (SDI)
092_12: H16.12, IC7.12 (SCK)
092_13: H16.13, IC7.13 (GND)
092_14: H16.14, IC7.14 (!CS)
092_15: H16.15, IC7.15 (!EN)
092_16: H16.16, IC7.16 (CLK)
092_17: H17.1, IC7.17 (SRB)
092_18: H17.2, IC7.18 (LB2)
092_19: H17.3, IC7.19 (LB1)
092_20: H17.4, IC7.20 (BMB1)
092_21: H17.5, IC7.21 (BMB2)
092_22: H17.6, IC7.22 (HB2)
092_23: H17.7, IC7.23 (HB1)
092_24: H17.8, IC7.24 (VHS)
092_25: H17.9, IC7.25 (VS)
092_26: H17.10, IC7.26 (TST_ANA)
092_27: H17.11, IC7.27 (SG_TST)
092_28: H17.12, IC7.28 (GND)
092_29: H17.13, IC7.29 (VCC_IO)
092_30: H17.14, IC7.30 (DIR)
092_31: H17.15, IC7.31 (STEP)
092_32: H17.16, IC7.32 (TST_MODE)
092_GND: IC7.EXP (DIE_PAD)
093_1: H15.1, IC8.1 (OA1)
093_2: H15.2, IC8.2 (OA1)
093_3: H15.3, IC8.3 (VBAT)
093_4: H15.4, IC8.4 (VBAT)
093_5: H15.5, IC8.5 (VBAT)
093_6: H15.6, IC8.6 (SWI)
093_7: H15.7, IC8.7 (UKN)
093_8: H15.8, IC8.8 (SDA)
093_9: H15.9, IC8.9 (SCL)
093_10: H15.10, IC8.10 (VDD)
093_11: H15.11, IC8.11 (GND)
093_12: H15.12, IC8.12 (TST)
093_13: H15.13, IC8.13 (OPEN)
093_14: H15.14, IC8.14 (GND)
093_15: H15.15, IC8.15 (HW)
093_16: H15.16, IC8.16 (UKN1)
093_17: H18.1, IC8.17 (CPN)
093_18: H18.2, IC8.18 (CPP)
093_19: H18.3, IC8.19 (VCP)
093_20: H18.4, IC8.20 (VBAT)
093_21: H18.5, IC8.21 (VBAT)
093_22: H18.6, IC8.22 (VBAT)
093_23: H18.7, IC8.23 (OB2)
093_24: H18.8, IC8.24 (OB2)
093_25: H18.9, IC8.25 (GND)
093_26: H18.10, IC8.26 (GND)
093_27: H18.11, IC8.27 (OB1)
093_28: H18.12, IC8.28 (OB1)
093_29: H18.13, IC8.29 (OA2)
093_30: H18.14, IC8.30 (OA2)
093_31: H18.15, IC8.31 (GND)
093_32: H18.16, IC8.32 (GND)
093_GND: IC8.EXP (DIE_PAD)
096_GND: IC9.P$49 (EXP)
100_1: H25.1, IC11.1 (TST_MODE)
100_2: H25.2, IC11.2 (CLK)
100_3: H25.3, IC11.3 (CSN_CFG3)
100_4: H25.4, IC11.4 (SCK_CFG2)
100_5: H25.5, IC11.5 (SDI_NAI_CFG1)
100_6: H25.6, IC11.6 (GND)
100_7: H25.7, IC11.7 (SDO_NAO_CFG0)
100_8: H25.8, IC11.8 (REFL_STEP)
100_9: H25.9, IC11.9 (REFR_DIR)
100_10: H25.10, IC11.10 (VCC_IO)
100_11: H25.11, IC11.11 (SD_MODE)
100_12: H25.12, IC11.12 (SPI_MODE)
100_13: H26.1, IC11.13 (GNDP)
100_14: H26.2, IC11.14
100_15: H26.3, IC11.15 (OB1)
100_16: H26.4, IC11.16
100_17: H26.5, IC11.17 (BRB)
100_18: H26.6, IC11.18
100_19: H26.7, IC11.19 (OB2)
100_20: H26.8, IC11.20
100_21: H26.9, IC11.21 (VS)
100_22: H26.10, IC11.22
100_23: H26.11, IC11.23 (ENCN_DCO)
100_24: H26.12, IC11.24 (ENCB_DCEN_CFG4)
100_25: H27.1, IC11.25 (ENCA_DCIN_CFG5)
100_26: H27.2, IC11.26 (SWN_DIAG0)
100_27: H27.3, IC11.27 (SWP_DIAG1)
100_28: H27.4, IC11.28 (SWSEL)
100_29: H27.5, IC11.29 (DRV_ENN_CFG6)
100_30: H27.6, IC11.30 (AIN_IREF)
100_31: H27.7, IC11.31
100_32: H27.8, IC11.32 (GNDA)
100_33: H27.9, IC11.33 (5VOUT)
100_34: H27.10, IC11.34 (VCC)
100_35: H27.11, IC11.35 (CPO)
100_36: H27.12, IC11.36
100_37: H28.1, IC11.37 (CPI)
100_38: H28.2, IC11.38 (VCP)
100_39: H28.3, IC11.39 (VSA)
100_40: H28.4, IC11.40
100_41: H28.5, IC11.41
100_42: H28.6, IC11.42 (OA2)
100_43: H28.7, IC11.43
100_44: H28.8, IC11.44 (BRA)
100_45: H28.9, IC11.45
100_46: H28.10, IC11.46 (OA1)
100_47: H28.11, IC11.47
100_48: H28.12, IC11.48
100_GND: IC11.PAD (GND_PAD)
unnamed: H20.1, IC9.P$1
unnamed: H20.2, IC9.P$2
unnamed: H20.3, IC9.P$3
unnamed: H20.4, IC9.P$4
unnamed: H20.5, IC9.P$5
unnamed: H20.6, IC9.P$6
unnamed: H20.7, IC9.P$7
unnamed: H20.8, IC9.P$8
unnamed: H20.9, IC9.P$9
unnamed: H20.10, IC9.P$10
unnamed: H20.11, IC9.P$11
unnamed: H20.12, IC9.P$12
unnamed: H21.1, IC9.P$13
unnamed: H21.2, IC9.P$14
unnamed: H21.3, IC9.P$15
unnamed: H21.4, IC9.P$16
unnamed: H21.5, IC9.P$17
unnamed: H21.6, IC9.P$18
unnamed: H21.7, IC9.P$19
unnamed: H21.8, IC9.P$20
unnamed: H21.9, IC9.P$21
unnamed: H21.10, IC9.P$22
unnamed: H21.11, IC9.P$23
unnamed: H21.12, IC9.P$24
unnamed: H23.1, IC9.P$25
unnamed: H23.2, IC9.P$26
unnamed: H23.3, IC9.P$27
unnamed: H23.4, IC9.P$28
unnamed: H23.5, IC9.P$29
unnamed: H23.6, IC9.P$30
unnamed: H23.7, IC9.P$31
unnamed: H23.8, IC9.P$32
unnamed: H23.9, IC9.P$33
unnamed: H23.10, IC9.P$34
unnamed: H23.11, IC9.P$35
unnamed: H23.12, IC9.P$36
unnamed: H22.1, IC9.P$37
unnamed: H22.2, IC9.P$38
unnamed: H22.3, IC9.P$39
unnamed: H22.4, IC9.P$40
unnamed: H22.5, IC9.P$41
unnamed: H22.6, IC9.P$42
unnamed: H22.7, IC9.P$43
unnamed: H22.8, IC9.P$44
unnamed: H22.9, IC9.P$45
unnamed: H22.10, IC9.P$46
unnamed: H22.11, IC9.P$47
unnamed: H22.12, IC9.P$48
SSOP2_1: H19.1, IC10.1 (REF1)
SSOP2_2: H19.2, IC10.2 (REF2)
SSOP2_3: H19.3, IC10.3 (REF3)
SSOP2_4: H19.4, IC10.4 (TEST)
SSOP2_5: H19.5, IC10.5 (CLK)
SSOP2_6: H19.6, IC10.6 (!SCS_C)
SSOP2_7: H19.7, IC10.7 (SCK_C)
SSOP2_8: H19.8, IC10.8 (SDI_C)
SSOP2_9: H24.1, IC10.9 (!INT!_SDO_C)
SSOP2_10: H24.2, IC10.10 (SDO_S_S1)
SSOP2_11: H24.3, IC10.11 (SCK_S_D1)
SSOP2_12: H24.4, IC10.12 (!SCS_S_S2)
SSOP2_13: H24.5, IC10.13 (V5)
SSOP2_14: H24.6, IC10.14 (V33)
SSOP2_15: H24.7, IC10.15 (GND)
SSOP2_16: H24.8, IC10.16 (SDI_S_D2)

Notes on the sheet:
Panel 1_2
TMC223-LI
QFN32 7x7mm
TMC249A-LA
TMC5031-LA TMC5062-LA TMC2031-LA TMC5041-LA
QFN48 7x7mm
TMC5130-PA TMC6131-PA
TQFP48-EP 7x7mm
TMC389-LA
QFN32 5x5mm
TMC429-LI
TMC4210
SSOP-16


Board: 2 copper layers, 160.0 x 100.0 mm, 55 parts (0 on the bottom side), 356 nets.

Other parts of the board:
U$1: TRINAMIC_LOGO
U$3, U$4, U$5, U$6, U$7, U$8, U$9, U$10, U$11, U$13, U$15, U$16: T-BONE_LOGO

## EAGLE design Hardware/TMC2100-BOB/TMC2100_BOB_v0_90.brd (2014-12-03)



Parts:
C1, C2, C6, C7: C0402/100nF/50V; C0402
C3: C0402/470nF/10V; C0402
C4: C0402/4.7uF/10V; C0402
C5: C0402/22nF/50V; C0402
C8: C0603/1uF/50V; C0603
JP1, JP2: PINHD-1X08_2.54-S; 1X08-S
R1: R0402/2R2; R0402
R2, R4: R0805/0R27; M0805
R3: TS53YJ103MR10; TS53YJ
R5: R0402/20k; R0402
U$1: TMC2100_QFN36; QFN36

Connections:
CFG1: JP1.7, U$1.4 (SDI_NAI_CFG1)
CFG2: JP1.6, U$1.3 (SCK_CFG2)
CFG3: JP1.5, U$1.2 (CSN_CFG3)
CFG6: JP1.8, U$1.22 (DRV_ENN_CFG6)
DIAG0: JP1.4, U$1.20 (SWN_DIAG0)
DIAG1: JP1.3, U$1.21 (SWP_DIAG1)
DIR: JP1.1, U$1.7 (REFR_DIR)
GND: C1.1, C2.2, C3.2, C4.2, C7.1, C8.2, JP2.2, JP2.8, R2.1, R3.3, R4.1, U$1.1 (CLK), U$1.10 (SPI_MODE), U$1.11 (GND), U$1.12 (GND), U$1.24 (GNDA), U$1.35 (GND), U$1.36 (TST_MODE), U$1.GND_PAD (GND)
unnamed: C3.1, R1.2, U$1.26 (VCC)
unnamed: C4.1, R1.1, U$1.25 (5VOUT)
unnamed: C6.1, U$1.29 (VCP)
unnamed: C5.1, U$1.28 (CPI)
unnamed: R4.2, U$1.33 (BRA)
unnamed: C5.2, U$1.27 (CPO)
unnamed: R2.2, U$1.14 (BRB)
unnamed: R3.1, R5.1
unnamed: R3.2, U$1.23 (AIN_IREF)
OA1: JP2.4, U$1.34 (OA1)
OA2: JP2.3, U$1.32 (OA2)
OB1: JP2.5, U$1.13 (OB1)
OB2: JP2.6, U$1.15 (OB2)
STEP: JP1.2, U$1.6 (REFL_STEP)
VM: C1.2, C6.2, C7.2, C8.1, JP2.1, U$1.16 (VS), U$1.30 (VSA), U$1.31 (VS)
V_IO: C2.1, JP2.7, R5.2, U$1.8 (VCC_IO)


Board: 4 copper layers, 15.2 x 20.3 mm, 16 parts (0 on the bottom side), 24 nets.

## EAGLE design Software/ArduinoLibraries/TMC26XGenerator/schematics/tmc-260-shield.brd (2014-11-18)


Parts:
A1, A2: M01PTH; 1X01
B1, B2: M01PTH; 1X01
BRA: M01PTH; 1X01
BRB: M01PTH; 1X01
C1, C2: Elko Panasonic G, 50V, EEEFC1H470P / EEEFK1H221P; CSV-G
C1': TTH alternative to C1; CE-035X100
C2': TTH alternative to C2; CE-035X100
C3, C4, C5, C8: 1µF,50V; C0603
C6: 10µF,50V; C1206
C7, C9, C10: 1µF; C0603
DIR: Yellow; MICRO-SIDELED
EN: Green; MICRO-SIDELED
IC1: TMC260-PA; PQFP44_WITH_PADS
J1: POWER_JACKPTH; POWER_JACK_PTH
JP1: M04SCREW; SCREWTERMINAL-3.5MM-4
JP2, JP5: M06SIP; 1X06
JP3: M05PTH; 1X05
JP4: M03PTH; 1X03
JP10, JP11, JP14: M01PTH; 1X01
PWR: Green; MICRO-SIDELED
Q1: BC856SOT323; SOT323-BEC
R1, R2: 10; R0603
R3, R4: 0,18; R2512
R6, R8, R10, R12, R14: 560; R0603
R7, R9, R11, R13: 10k; R0603
R15: 1k; R0603
R16, R17, R18: 100k; R0603
RESET: TAC_SWITCHSMD; TACTILE_SWITCH_SMD
SG: Red; MICRO-SIDELED
SJ1: SOLDERJUMPERNO; SJ_2S-NO
STEP: Yellow; MICRO-SIDELED
T2, T3, T4: BC850SOT323; SOT323-BEC
U$1: ARDUINOUNO; ARDUINO
U$10: KK4H; KK-H-4
VMOT: M021X02_NO_SILK; 1X02_NO_SILK

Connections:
3V: U$1.3V
5V: C8.2, DIR.A, Q1.E, SG.A, STEP.A, U$1.5V
5VOUT: C9.2, C10.2, IC1.13 (5VOUT), IC1.40 (VCC_IO), PWR.A, R18.2
!CS: IC1.18 (!CS), JP3.5, R18.1
!EN: IC1.19 (!EN), JP3.1, R7.1, R15.1
A1: A1.1, IC1.2 (OA1), IC1.7 (OA1), JP1.1, U$10.1
A2: A2.1, IC1.5 (OA2), IC1.10 (OA2), JP1.2, U$10.2
B1: B1.1, IC1.26 (OB1), IC1.31 (OB1), JP1.3, U$10.3
B2: B2.1, IC1.23 (OB2), IC1.28 (OB2), JP1.4, U$10.4
DIR: IC1.41 (DIR), JP3.3, R11.1, R17.1
GND: C1.-, C1'.-, C2.-, C2'.-, C3.1, C4.1, C5.1, C6.1, C8.1, C9.1, C10.1, IC1.17 (GND), IC1.21 (CLK), IC1.39 (GND), IC1.43 (TST_MODE), IC1.44 (GND), J1.GND, J1.GNDBREAK, JP10.1, JP11.1, JP14.1, R3.1, R4.1, R6.1, R8.1, R10.1, R12.1, R14.1, R15.2, R16.2, R17.2, RESET.1, RESET.2, U$1.GND, U$1.GND1, U$1.GND2
MISO: IC1.14 (SDO), U$1.D12
MOSI: IC1.15 (SDI), U$1.D11
unnamed: JP4.1, U$1.D10
unnamed: JP4.2, U$1.D9
unnamed: JP4.3, U$1.D8
unnamed: JP2.1, U$1.D7
unnamed: JP2.2, U$1.D6
unnamed: JP2.3, U$1.D5
unnamed: JP2.4, U$1.D4
unnamed: JP2.5, U$1.D3
unnamed: JP2.6, U$1.D2
unnamed: JP5.1, U$1.A5
unnamed: JP5.2, U$1.A4
unnamed: JP5.3, U$1.A3
unnamed: JP5.4, U$1.A2
unnamed: JP5.5, U$1.A1
unnamed: JP5.6, U$1.A0
unnamed: R9.2, T2.B
unnamed: RESET.3, RESET.4, U$1.RESET (/RESET)
unnamed: SJ1.1, U$1.VIN
unnamed: STEP.C, T2.C
unnamed: R10.2, T2.E
unnamed: PWR.C, R6.2
unnamed: R11.2, T3.B
unnamed: DIR.C, T3.C
unnamed: R12.2, T3.E
unnamed: EN.A, Q1.C
unnamed: BRA.1, IC1.9 (BRA), R1.2, R3.2
unnamed: IC1.12 (SRA), R1.1
unnamed: BRB.1, IC1.25 (BRB), R2.2, R4.2
unnamed: IC1.22 (SRB), R2.1
unnamed: EN.C, R8.2
unnamed: Q1.B, R7.2
unnamed: R13.2, T4.B
unnamed: SG.C, T4.C
unnamed: R14.2, T4.E
SCK: IC1.16 (SCK), U$1.D13
SG: IC1.38 (SG_TST), JP3.4, R13.1
STEP: IC1.42 (STEP), JP3.2, R9.1, R16.1
VCC: C1.+, C1'.+, C2.+, C2'.+, C3.2, C4.2, C5.2, C6.2, C7.2, IC1.4 (VSA), IC1.30 (VSB), IC1.36 (VS), J1.PWR, SJ1.2, VMOT.1, VMOT.2
VHS: C7.1, IC1.35 (VHS)

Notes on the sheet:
TOS-100 Arduino Shield
This work is licensed under a Creative Commons Attribution 3.0 Germany License. http://creativecommons.org/licenses/by/3.0/de/deed.en_US


Board: 2 copper layers, 68.6 x 53.3 mm, 64 parts (0 on the bottom side), 51 nets.

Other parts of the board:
U$5: LOGO
U$9: COOLSTEP
U$11: OSHW_FILLX200_NOTEXT
U$12: SMALL_LOGO_COPPER
U$13: QR-TMC-100-BOTTOM-BIG

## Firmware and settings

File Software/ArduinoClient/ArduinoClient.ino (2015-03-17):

#include <avr/interrupt.h>
#include <digitalIOPerformance.h>
#include <SPI.h>
#include <QueueArray.h>
#include <TMC26XGenerator.h>
#include <CmdMessenger.h>

#include "constants.h"
#include "types.h"

//##################
//# Debug Settings #
//##################

//#define DEBUG_MOTOR_CONTFIG
//#define DEBUG_HOMING
//#define BUG_HOMING_STATUS
//#define DEBUG_HOMING_STATUS_5041
//#define DEBUG_ENDSTOPS
//#define DEBUG_ENDSTOPS_DETAIL

//#define DEBUG_MOTION
//#define DEBUG_MOTION_SHORT
//#define DEBUG_MOTION_TRACE
//#define DEBUG_MOTION_TRACE_SHORT
//#define DEBUG_MOTION_START
//#define DEBUG_MOTION_REGISTERS
//#define DEBUG_MOTOR_QUEUE
//#define DEBUG_MOTION_STATUS
//#define DEBUG_SET_POS
//#define DEBUG_MOTOR_CONTFIG

//#define DEBUG_SPI

//#define DEBUG_STATUS
//#define DEBUG_STATUS_SHORT
//#define DEBUG_TMC5041_STATUS
//#define DEBUG_TMC4361_STATUS

//#define RX_TX_BLINKY
//#define RX_TX_BLINKY_1

//how many motors do we know?
const char nr_of_coordinated_motors = 3;
const char nr_of_controlled_motors = 2;
const char nr_of_motors = nr_of_coordinated_motors + nr_of_controlled_motors;
const char homing_max_following_motors = nr_of_controlled_motors - 1;

//how much space do we have to store commands
#define COMMAND_QUEUE_LENGTH 40

//standards
#define TMC_260_CONFIG 0x8440000a //SPI-Out: block/low/high_time=8/4/4 Takte; CoverLength=autom; TMC26x
#define TMC260_SENSE_RESISTOR_IN_MO 100
#define CLOCK_FREQUENCY 16000000ul
#define DEFAULT_CURRENT_IN_MA 10
#define DEFAULT_STEPS_PER_REVOLUTION 200

#define DEFAULT_ACCELERATION 1
#define DEFAULT_BOW 1

//#define CALCULATE_OUTPUT TXLED
//the CS pins have to be defines for digitalWriteFast 
#define CS_4361_1_PIN 4
#define CS_4361_2_PIN 12
#define CS_4361_3_PIN 6
#define START_SIGNAL_PIN A3
#define CS_5041_PIN 11

#define INT_5041_PIN 8
#define INT_4361_1_PIN 3
#define INT_4361_2_PIN 2
#define INT_4361_3_PIN 7

#define PWM1_PIN 9
#define PWM2_PIN 10
#define PWM3_PIN 5

#define TEMP1_PIN A0
#define TEMP2_PIN A1
#define TEMP3_PIN A2

#define FB1_PIN A4
#define FB2_PIN A5

TMC4361_info motors[nr_of_coordinated_motors] = {
  {
    INT_4361_1_PIN,0, motor_1_target_reached, 
    TMC26XGenerator(DEFAULT_CURRENT_IN_MA,TMC260_SENSE_RESISTOR_IN_MO),
    DEFAULT_STEPS_PER_REVOLUTION                    }
  ,
  {
    INT_4361_2_PIN,1, motor_2_target_reached, 
    TMC26XGenerator(DEFAULT_CURRENT_IN_MA,TMC260_SENSE_RESISTOR_IN_MO), 
    DEFAULT_STEPS_PER_REVOLUTION                     }
  ,
  {
    INT_4361_3_PIN,4, motor_3_target_reached, 
    TMC26XGenerator(DEFAULT_CURRENT_IN_MA,TMC260_SENSE_RESISTOR_IN_MO), 
    DEFAULT_STEPS_PER_REVOLUTION                     }
};


#define DEFAULT_COMMAND_BUFFER_DEPTH (nr_of_motors)

//how many otors can be theoretically geared together
#define MAX_FOLLOWING_MOTORS (nr_of_motors-1)


motion_state current_motion_state = no_motion;
//this bitfiled store which motors are invesed - _BV(1) means the motor is inversed)
unsigned char inverted_motors;



volatile boolean next_move_prepared = false;
volatile boolean move_executing = false;
//volatile unsigned int motor_status;
//volatile unsigned char target_motor_status;
//volatile unsigned char next_target_motor_status;
volatile unsigned char differential_encoder_motors;
char direction[nr_of_coordinated_motors];
char next_direction[nr_of_coordinated_motors];
unsigned char min_buffer_depth = DEFAULT_COMMAND_BUFFER_DEPTH;


//config

QueueArray<movement> moveQueue = QueueArray<movement>(COMMAND_QUEUE_LENGTH);


//somebody must deal with our commands
CmdMessenger messenger = CmdMessenger(Serial1);

void setup() {
  //pwm is done in the bbb
  pinModeFast(PWM1_PIN,OUTPUT);
  digitalWriteFast(PWM1_PIN,LOW);
  pinModeFast(PWM2_PIN,OUTPUT);
  digitalWriteFast(PWM2_PIN,LOW);
  pinModeFast(PWM3_PIN,OUTPUT);
  digitalWriteFast(PWM3_PIN,LOW);

  //switch the analog pins as innput to hand them over to the BBB
  pinModeFast(TEMP1_PIN,INPUT);
  digitalWriteFast(TEMP1_PIN,LOW);
  pinModeFast(TEMP2_PIN,INPUT);
  digitalWriteFast(TEMP2_PIN,LOW);
  pinModeFast(TEMP3_PIN,INPUT);
  digitalWriteFast(TEMP3_PIN,LOW);
  pinModeFast(FB1_PIN,INPUT);
  digitalWriteFast(FB1_PIN,LOW);
  pinModeFast(FB1_PIN,INPUT);
  digitalWriteFast(FB1_PIN,LOW);

  //initialize SPI
  SPI.begin();
  SPI.setBitOrder(MSBFIRST);
  SPI.setDataMode(SPI_MODE3);
  SPI.setClockDivider(SPI_CLOCK_DIV4);
//  SPI.setClockDivider(SPI_CLOCK_DIV2);

  // Use HWBE as Output
  DDRE |= _BV(2);                    // set HWBE pin as output (Fuse HWBE disabled, point to check..)

  // Analog reference AREF
  analogReference(EXTERNAL);

  //initialize the serial port for commands
  Serial1.begin(38400);
  Serial.begin(115200);

  //at least we should try deactivate the motion drivers
  resetTMC4361(true, true);

  //set the TMC4361 ipns correctly
  prepareTMC4361();
  
  //set the TMMC5041 pins correctly
  prepareTMC5041();

  //set the serial as debug output 
  moveQueue.setStream(Serial);

#ifdef CALCULATE_OUTPUT
  pinModeFast(CALCULATE_OUTPUT, OUTPUT);
  digitalWriteFast(CALCULATE_OUTPUT,LOW);
#endif

  // Adds newline to every command
  messenger.printLfCr();   

  // Attach my application's user-defined callback methods
  attachCommandCallbacks();

  //finally signal that we are ready
  watchDogStart();
}

unsigned long last_millis=0;

void loop() {
//  static char loopidx = 0; // this was a test to give the communication a lower priority

//  if (loopidx < 10) {
//    loopidx++;
    //move if neccessary
    checkMotion();
//  } else {
    // Process incoming serial data, and perform callbacks
    messenger.feedinSerialData();
//    loopidx = 0;
//  } 

  if (millis()-last_millis>1000) {
#ifdef RX_TX_BLINKY
    TXLED1;
#endif
    watchDogPing();
    last_millis=millis();
#ifdef RX_TX_BLINKY
    TXLED0;
#endif
  }
}

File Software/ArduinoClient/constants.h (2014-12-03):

//hard coded value
#define MAX_MOTOR_CURRENT_260 2000
#define MAX_MOTOR_CURRENT_5041 1000

//registers for TMC4361
#define TMC4361_GENERAL_CONFIG_REGISTER 0x0
#define TMC4361_REFERENCE_CONFIG_REGISTER 0x01
#define TMC4361_START_CONFIG_REGISTER 0x2
#define TMC4361_INPUT_FILTER_REGISTER 0x3
#define TMC4361_SPIOUT_CONF_REGISTER 0x04
#define TMC4361_ENCODER_INPUT_CONFIG_REGISTER 0x07
#define TMC4361_STEP_CONF_REGISTER 0x0A
#define TMC4361_EVENT_CLEAR_CONF_REGISTER 0x0c
#define TMC4361_INTERRUPT_CONFIG_REGISTER 0x0d
#define TMC4361_EVENTS_REGISTER 0x0e
#define TMC4361_STATUS_REGISTER 0x0f
#define TMC4361_START_OUT_ADD_REGISTER 0x11
#define TMC4361_GEAR_RATIO_REGISTER 0x12
#define TMC4361_START_DELAY_REGISTER 0x13
#define TMC4361_RAMP_MODE_REGISTER 0x20
#define TMC4361_X_ACTUAL_REGISTER 0x21 
#define TMC4361_V_ACTUAL_REGISTER 0x22
#define TMC4361_A_ACTUAL_REGISTER 0x23
#define TMC4361_V_MAX_REGISTER 0x24
#define TMC4361_V_START_REGISTER 0x25
#define TMC4361_V_STOP_REGISTER 0x26
#define TMC4361_A_MAX_REGISTER 0x28
#define TMC4361_D_MAX_REGISTER 0x29
#define TMC4361_BOW_1_REGISTER 0x2d
#define TMC4361_BOW_2_REGISTER 0x2e
#define TMC4361_BOW_3_REGISTER 0x2f
#define TMC4361_BOW_4_REGISTER 0x30
#define TMC4361_CLK_FREQ_REGISTER 0x31
#define TMC4361_POSITION_COMPARE_REGISTER 0x32
#define TMC4361_VIRTUAL_STOP_LEFT_REGISTER 0x33
#define TMC4361_VIRTUAL_STOP_RIGHT_REGISTER 0x34
#define TMC4361_X_LATCH_REGISTER 0x36
#define TMC4361_X_TARGET_REGISTER 0x37
#define TMC4361_X_TARGET_PIPE_0_REGSISTER 0x38
#define TMC4361_SH_V_MAX_REGISTER 0x40
#define TMC4361_SH_A_MAX_REGISTER 0x41
#define TMC4361_SH_D_MAX_REGISTER 0x42
#define TMC4361_SH_VBREAK_REGISTER 0x45
#define TMC4361_SH_V_START_REGISTER 0x46
#define TMC4361_SH_V_STOP_REGISTER 0x47
#define TMC4361_SH_BOW_1_REGISTER 0x48
#define TMC4361_SH_BOW_2_REGISTER 0x49
#define TMC4361_SH_BOW_3_REGISTER 0x4A
#define TMC4361_SH_BOW_4_REGISTER 0x4B
#define TMC4361_SH_RAMP_MODE_REGISTER 0x4C
#define TMC4361_ENCODER_POSITION_REGISTER 0x50
#define TMC4361_ENCODER_INPUT_RESOLUTION_REGISTER 0x54
#define TMC4361_COVER_LOW_REGISTER 0x6c
#define TMC4361_COVER_HIGH_REGISTER 0x6d

//registers for TMC5041
#define TMC5041_GENERAL_CONFIG_REGISTER 0x00
#define TMC5041_GENERAL_STATUS_REGISTER 0x01
#define TMC5041_INPUT_REGISTER 0x04

#define TMC5041_RAMP_MODE_REGISTER_1 0x20
#define TMC5041_X_ACTUAL_REGISTER_1 0x21
#define TMC5041_V_ACTUAL_REGISTER_1 0x22
#define TMC5041_V_START_REGISTER_1 0x23
#define TMC5041_A_1_REGISTER_1 0x24
#define TMC5041_V_1_REGISTER_1 0x25
#define TMC5041_A_MAX_REGISTER_1 0x26
#define TMC5041_V_MAX_REGISTER_1 0x27
#define TMC5041_D_MAX_REGISTER_1 0x28
#define TMC5041_D_1_REGISTER_1 0x2a
#define TMC5041_V_STOP_REGISTER_1 0x2b
#define TMC5041_T_ZERO_WAIT_REGISTER_1 0x2c
#define TMC5041_X_TARGET_REGISTER_1 0x2d
#define TMC5041_HOLD_RUN_CURRENT_REGISTER_1 0x30
#define TMC5041_REFERENCE_SWITCH_CONFIG_REGISTER_1 0x34
#define TMC5041_X_LATCH_REGISTER_1 0x36
#define TMC5041_RAMP_STATUS_REGISTER_1 0x35
#define TMC5041_CHOPPER_CONFIGURATION_REGISTER_1 0x6c
#define TMC5041_DRIVER_STATUS_REGISTER_1 0x6f

#define TMC5041_RAMP_MODE_REGISTER_2 0x40
#define TMC5041_X_ACTUAL_REGISTER_2 0x41
#define TMC5041_V_ACTUAL_REGISTER_2 0x42
#define TMC5041_V_START_REGISTER_2 0x43
#define TMC5041_A_1_REGISTER_2 0x44
#define TMC5041_V_1_REGISTER_2 0x45
#define TMC5041_A_MAX_REGISTER_2 0x46
#define TMC5041_V_MAX_REGISTER_2 0x47
#define TMC5041_D_MAX_REGISTER_2 0x48
#define TMC5041_D_1_REGISTER_2 0x4a
#define TMC5041_V_STOP_REGISTER_2 0x4b
#define TMC5041_T_ZERO_WAIT_REGISTER_2 04c
#define TMC5041_X_TARGET_REGISTER_2 0x4d
#define TMC5041_HOLD_RUN_CURRENT_REGISTER_2 0x50
#define TMC5041_REFERENCE_SWITCH_CONFIG_REGISTER_2 0x54
#define TMC5041_X_LATCH_REGISTER_2 0x56
#define TMC5041_RAMP_STATUS_REGISTER_2 0x55
#define TMC5041_CHOPPER_CONFIGURATION_REGISTER_2 0x7c
#define TMC5041_DRIVER_STATUS_REGISTER_2 0x7f

//a nice define to address the TMC5041
#define TMC5041_MOTORS 3

//standard values
#define I_HOLD_DELAY 2
#define V_LOW_SENSE 0.325
#define V_HIGH_SENSE 0.18
#define SQRT_2 (1.414213562373095)
#define TMC_5041_R_SENSE 0.29        // Lars: 270mOhm + 20mOhm from datasheet on electronic

//some nice calculation s
//simple FP math see https://ucexperiment.wordpress.com/2012/10/28/fixed-point-math-on-the-arduino-platform/
#define FIXED_23_8_MAKE(a)     (int32_t)((a*(1ul << 8ul)))
#define FIXED_22_2_MAKE(a)     (int32_t)((a*(1ul << 2ul)))

#define X_TARGET_IN_DIRECTION(m,t) ((inverted_motors & _BV(m))? -t:t)
#define IS_COORDINATED_MOTOR(a) (a<nr_of_coordinated_motors)
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

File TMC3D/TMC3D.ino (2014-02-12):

#include <SPI.h>
#include <TMC26XGenerator.h>

// TMC4361 registers
#define GENERAL_CONFIG_REGISTER 0x0
#define START_CONFIG_REGISTER 0x2
#define SPIOUT_CONF_REGISTER 0x04
#define STEP_CONF_REGISTER 0x0A
#define RAMP_MODE_REGISTER 0x20
#define V_MAX_REGISTER 0x24
#define A_MAX_REGISTER 0x28
#define D_MAX_REGISTER 0x29
#define BOW_1_REGISTER 0x2d
#define BOW_2_REGISTER 0x2e
#define BOW_3_REGISTER 0x2f
#define BOW_4_REGISTER 0x30
#define CLK_FREQ_REGISTER 0x31
#define X_TARGET_REGISTER 0x37
#define COVER_LOW_REGISTER 0x6c
#define COVER_HIGH_REGISTER 0x6d

#define REFERENCE_CONFIG_REGISTER 0x01
#define VIRTUAL_STOP_LEFT_REGISTER 0x33
#define VIRTUAL_STOP_RIGHT_REGISTER 0x34
#define EVENTS_REGISTER 0x0e
#define STATUS_REGISTER 0x0f
#define X_ACTUAL_REGISTER 0x21
#define X_LATCH_REGISTER 0x36

// TMC2660 registers
#define TMC_26X_CONFIG 0x8440000a //SPI-Out: block/low/high_time=8/4/4 Takte; CoverLength=autom; TMC26x
#define TMC260_SENSE_RESISTOR_IN_MO 100
#define CLOCK_FREQUENCY 16000000ul

// TMC5031 registers
#define TMC5031_GENERAL_CONFIG_REGISTER 0x00
#define TMC5031_GENERAL_STATUS_REGISTER 0x01
#define TMC5031_INPUT_REGISTER 0x04

#define TMC5031_RAMP_MODE_REGISTER_1 0x20
#define TMC5031_X_ACTUAL_REGISTER_1 0x21
#define TMC5031_V_ACTUAL_REGISTER_1 0x22
#define TMC5031_A_1_REGISTER_1 0x24
#define TMC5031_V_1_REGISTER_1 0x25
#define TMC5031_A_MAX_REGISTER_1 0x26
#define TMC5031_V_MAX_REGISTER_1 0x27
#define TMC5031_D_MAX_REGISTER_1 0x28
#define TMC5031_D_1_REGISTER_1 0x29a
#define TMC5031_V_STOP_REGISTER_1 0x29b
#define TMC5031_X_TARGET_REGISTER_1 0x2d
#define TMC5031_HOLD_RUN_CURRENT_REGISTER_1 0x30
#define TMC5031_REFERENCE_SWITCH_CONFIG_REGISTER_1 0x34
#define TMC5031_RAMP_STATUS_REGISTER_2 0x35
#define TMC5031_CHOPPER_CONFIGURATION_REGISTER_1 0x6c
#define TMC5031_DRIVER_STATUS_REGISTER_1 0x6f

#define TMC5031_RAMP_MODE_REGISTER_2 0x40
#define TMC5031_X_ACTUAL_REGISTER_2 0x41
#define TMC5031_V_ACTUAL_REGISTER_2 0x42
#define TMC5031_A_1_REGISTER_2 0x44
#define TMC5031_V_1_REGISTER_2 0x45
#define TMC5031_A_MAX_REGISTER_2 0x46
#define TMC5031_V_MAX_REGISTER_2 0x47
#define TMC5031_D_MAX_REGISTER_2 0x48
#define TMC5031_D_1_REGISTER_2 0x4a
#define TMC5031_V_STOP_REGISTER_2 0x49b
#define TMC5031_X_TARGET_REGISTER_2 0x4d
#define TMC5031_HOLD_RUN_CURRENT_REGISTER_2 0x50
#define TMC5031_REFERENCE_SWITCH_CONFIG_REGISTER_2 0x54
#define TMC5031_RAMP_STATUS_REGISTER_2 0x55
#define TMC5031_CHOPPER_CONFIGURATION_REGISTER_2 0x7c
#define TMC5031_DRIVER_STATUS_REGISTER_2 0x7f

#define DEBUG
#define CLK_FREQ 16000000ul

// Define Chip select Output
#define CS_5041_PIN 11
#define CS_4361_1_PIN 4
#define CS_4361_2_PIN 12
#define CS_4361_3_PIN 6

// Define PWM Output
#define PWM1_PIN 9
#define PWM2_PIN 10
#define PWM3_PIN 5
int pwmTime = 0;
int pwmStep = 5;

// Define analog TEMP inputs
#define TEMP1_PIN A0                    // Analog 0
#define TEMP2_PIN A1                    // Analog 1
#define TEMP3_PIN A2                    // Analog 2
#define FEEDBACK1_PIN A4                // Analog 4
#define FEEDBACK2_PIN A5                // Analog 5

// Define other signals
#define INT_5041_PIN 8
#define INT_4361_1_PIN 3
#define INT_4361_2_PIN 2
#define INT_4361_3_PIN 7
#define START_PIN A3

// TMC5041
unsigned int AMP5041 = 200;
unsigned int holdAMP5041 = 100;
unsigned long chopper_config;
unsigned long current_register;

#define TMC_5031_R_SENSE 0.27
#define I_HOLD_DELAY 2

// TMC4361
unsigned char steps_per_revolution = 200;
unsigned int AMP4361 = 500;
long vmax = 100000000ul;
long bow = 1000000;
long end_bow = bow;
long amax = vmax/100;
long dmax = amax;

// TMC2660
TMC26XGenerator tmc260 = TMC26XGenerator(AMP4361, TMC260_SENSE_RESISTOR_IN_MO);

unsigned char status;

void setup()
{
  // Analog reference AREF
  analogReference(EXTERNAL);
  
  // Config SPI (CPOL = 1 and CPHA = 1)
  //SPI.setBitOrder(MSBFIRST);              // MSB sent first (TMC)
  //SPI.setClockDivider(SPI_CLOCK_DIV4);    // At 16MHz CLK = 4MHz
  //SPI.setDataMode(SPI_MODE3);             // Set CPOL=1 and CPHA=1
  SPI.begin();
  Serial.begin(9600);
  
  // Set CS IOs
  pinMode(CS_5041_PIN, OUTPUT);
  digitalWrite(CS_5041_PIN, LOW);
  pinMode(CS_4361_1_PIN, OUTPUT);
  digitalWrite(CS_4361_1_PIN, LOW);
  pinMode(CS_4361_2_PIN, OUTPUT);
  digitalWrite(CS_4361_2_PIN, LOW);
  pinMode(CS_4361_3_PIN, OUTPUT);
  digitalWrite(CS_4361_3_PIN, LOW);
  
  // Set PWM IOs
  pinMode(PWM1_PIN, OUTPUT);
  digitalWrite(PWM1_PIN, LOW);
  pinMode(PWM2_PIN, OUTPUT);
  digitalWrite(PWM2_PIN, LOW);
  pinMode(PWM3_PIN, OUTPUT);
  digitalWrite(PWM3_PIN, LOW);
  
  // Set other IOs
  pinMode(INT_5041_PIN, INPUT);
  pinMode(INT_4361_1_PIN, INPUT);
  pinMode(INT_4361_2_PIN, INPUT);
  pinMode(INT_4361_3_PIN, INPUT);
  pinMode(START_PIN, OUTPUT);

  // motor config
  unsigned long motorconfig = 0x00; //we want 256 microsteps
  motorconfig |= steps_per_revolution << 4;
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

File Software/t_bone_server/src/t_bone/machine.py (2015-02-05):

# coding=utf-8
from Queue import Queue, Empty
import logging
import re
from threading import Thread
import serial
import threading
import time
from math import floor
import Adafruit_BBIO.GPIO as GPIO

__author__ = 'marcus'

_default_timeout = 120
_commandEndMatcher = re.compile(";")  # needed to search for command ends
_min_command_buffer_free_space = 5  # how much arduino buffer to preserve
_initial_buffer_length = 20  # how much buffer do we need befoer starting to print
_buffer_empyting_wait_time = 0.05
_buffer_warn_waittime = 10
clock_frequency = 16000000

_logger = logging.getLogger(__name__)

MAXIMUM_FREQUENCY_ACCELERATION = 2 ** 22 - 2
MAXIMUM_FREQUENCY_BOW = 2 ** 24 - 2


class Machine():
    def __init__(self, serial_port, reset_pin):
        # preapre the reset pin
        self.reset_pin = reset_pin
        _logger.debug("Defining ports & pins")
        GPIO.setup(self.reset_pin, GPIO.OUT)
        GPIO.output(self.reset_pin, GPIO.HIGH)
        self.serial_port = serial_port
        self.remaining_buffer = ""
        self.machine_connection = None
        self.command_queue = Queue()
        self.batch_mode = False

    def connect(self):
        _logger.info("resetting arduino at %s", self.serial_port)
        GPIO.output(self.reset_pin, GPIO.LOW)
        # reset the arduino
        time.sleep(1)
        GPIO.output(self.reset_pin, GPIO.HIGH)
        time.sleep(15)
        _logger.info("waiting for arduino")
        if not self.machine_connection:
            machineSerial = serial.Serial(self.serial_port, 38400, timeout=_default_timeout)
            self.machine_connection = _MachineConnection(machineSerial)
        init_command = MachineCommand()
        init_command.command_number = 9
        reply = self.machine_connection.send_command(init_command)
        if reply.command_number != 0:
            _logger.fatal("Unable to start, received %s which is not OK", reply)
            raise MachineError("Unable to start")

    def disconnect(self):
        if self.machine_connection:
            self.machine_connection.stop()

    def set_current(self, motor=None, current=None):
        command = MachineCommand()
        command.command_number = 1
        command.arguments = (
            int(motor),
            int(current * 1000)
        )
        reply = self.machine_connection.send_command(command)
        if not reply or reply.command_number != 0:
            _logger.fatal("Unable to set motor current:%s", reply)
            raise MachineError("Unable to set motor current", reply)

    def invert_motor(self, motor=None, inverted=False):
        command = MachineCommand()
        command.command_number = 4
        if inverted:
            invert_value = -1
        else:
            invert_value = 1
        command.arguments = (
            int(motor),
            invert_value
        )
        reply = self.machine_connection.send_command(command)
        if not reply or reply.command_number != 0:
            _logger.fatal("Unable to set motor current:%s", reply)
            raise MachineError("Unable to invert motor", reply)

    def configure_encoder(self, motor, encoder_config):
        if encoder_config:
            # enable the encoder
            if encoder_config['differential']:
                differential_value = 1
            else:
                differential_value = -1
            if encoder_config['inverted']:
                inverted_value = 1
            else:
                inverted_value = -1
            arguments = (
                int(motor),
                1,  # enable
                int(encoder_config['steps-per-rev']),
                256,  # todo this CAN be different …
                int(encoder_config['increments-per-rev']),
                differential_value,
                inverted_value
            )
        else:
            arguments = (
                int(motor),
                -1,  # disable
                0,
                0,
                0
            )
        command = MachineCommand()
        command.command_number = 2
        command.arguments = arguments
        reply = self.machine_connection.send_command(command)
        if not reply:
            _logger.fatal("Unable to configure encoder")
            raise MachineError("Unable to configure encoder")

    def configure_endstop(self, motor, position, end_stop_config):
        command = MachineCommand()
        command.command_number = 3

        type = end_stop_config['type']
        position = position
        if position == 'left':
            position_number = -1
        else:
            position_number = 1

        if type == 'real':
            polarity = end_stop_config['polarity']
            if polarity in ('negative', '-', 'neg'):
                polarity_token = -1
            else:
                polarity_token = 1

            command.arguments = (
                int(motor),
                position_number,
                1,  # 1 is a real endstop
                polarity_token
            )
        else:
            command.arguments = (
                int(motor),
                position_number,
                0,  # 1 is a virtual endstop
                int(end_stop_config['position'])
            )

        # send the command
        reply = self.machine_connection.send_command(command)
        if not reply or reply.command_number != 0:
            _logger.fatal("Unable to configure end stops :%s", reply)
            raise MachineError("Unable to configure end stops", reply)

    def home(self, home_config, timeout):
        command = MachineCommand()
        command.command_number = 12
        if 'jerk' in home_config:
            # TODO why so complicated? can't it be integrated with the addition code later on ?
            jerk = int(home_config['jerk'])
        else:
            jerk = None
        if 'followers' in home_config:
            # we lazily add the motor in the printer - since it is quite easy to remove it here
            following = [motor for motor in home_config['followers'] if motor != home_config['motor']]
        else:
            following = None

        command.arguments = [
            int(home_config['motor']),
            int(home_config['timeout']),
            float(home_config['home_speed']),
            float(home_config['home_slow_speed']),
            int(home_config['home_retract']),
            float(home_config['acceleration']),
        ]
        # if jerk:
        #     command.arguments.append(jerk)
        if following:
            for motor in following:
                command.arguments.append(int(motor))
        if 'homing_right_position' in home_config:
            command.arguments.append(int(home_config['homing_right_position']))
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

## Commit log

2000-01-01 added encoder into web-ui, added autoservice and changed http port from 5000 to 80
2000-01-01 this is the correct led stuff
    [printer.py]
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2013-10-24 ok, this is what we test tomorrow …
    … it should configure the TMC260
2013-10-25 cleaning up for motor config
    separate read/write are easier to understand
    _REGISTER my help to identify defines
2013-10-25 ok, now starrting the motor
    and fixing the sense resistors
2013-10-25 slightly less current to avoid damages & injuries
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2013-10-25 perhaps it just did not move because it accelerated too slow …
2013-10-28 ah yea, there are just 50 callbacks …
    perhaps we have to change this later …
2013-10-28 messaging rework
    and ready …
    [ArduinoClient.ino, Commands.ino]
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2013-10-29 resetting in the final sketch too …
    [ArduinoClient.ino, TMC43x.ino]
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2013-10-29 oops, we should return null to indicate that there was no error
    [TMC43x.ino]
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2013-10-30 fixed point math is not that hard …
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2013-10-31 ok, now we use pipelines, but do not move due to misconfiguration …
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2013-10-31 why doesn't the start pin work??
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2013-11-04 setting the acccleration for the 2nd (or 1st) motor helps a lot
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2013-11-05 ok, this isthe final version of how to use shaddow reigsters
    _BV(5) in start config did the trick …
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2013-11-05 we do want an queue of a fixed length
    [ArduinoClient.ino, Commands.ino]
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2013-11-05 we should return in case of errors
    [Commands.ino]
2013-11-07 hmm, a union may be a bit more organized …
    and setting vmax to float … might not survive long
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2013-11-07 hmm, a dedicated command to read back queue length is nice …
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2013-11-11 ok it seems that we have logging and some basic optiona management … now let's see how we can combine its
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2013-11-11 hmm, if there is an logging problem let's chek the command line
    [Machine.py]
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2013-11-12 ok, we need a proper connect and poper return codes and os on …
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2013-11-12 missing brackets??
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2013-11-12 this won't work (silly mistake)
    [Machine.py]
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2013-11-12 ok, this seem to work - but we have to flush the input buffer first …
2013-11-13 ok, after one o another fight the basic communication is there …
2013-11-13 we should note the internal parameters and values … store it in the script
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2013-11-13 the calibration object is rather simple
    even though if it is not clear if it is big enough …
    [test-model.scad, test-model.stl]
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2013-11-14 ok, this is the basic sketch of the move function - w/o the move itself …
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2013-11-15 this will hilgh levely move the motors
    if we will ever succeed abstracting it …
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2013-11-18 ok, this is more or less the motion planning …
    or at least a beginning
2013-11-18 adding some fixed point math to the mix
    [constants.h]
2013-11-18 some minor corrections (start interrupt)
    [ArduinoClient.ino, Motion.ino, TMC43x.ino]
2013-11-18 ok, let's start slowy …
    … just moving the motors according to the queue
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2013-11-18 it might come in handy to have a dedicated start/stop print method
2013-11-18 we need to start if the buffer is full and not overfill it …
2013-11-18 at least it should move now … so why doesn't it do it??
    [Commands.ino, Machine.py]
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2013-11-19 after some corrections it works
    to wait for movements
    [Commands.ino, Machine.py]
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2013-11-19 at least we already know if the next movment will be with the same leading motor
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2013-11-19 hmm bigger acceleration gave problems
    a) it was read as int
    b) the unit conversion was not active for speed
    [Commands.ino]
2013-11-19 ok, we are chainnig the motor commands …
    … even if the master is switching
2013-11-19 fixing the gearing caalcuation
2013-11-20 we will need some helper methods for analyzing the speed vectors …
2013-11-20 with movment vectors we can calucate on r another thing differently …
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2013-11-20 we cannot react to errors anyway …
    [TMC43x.ino]
2013-11-20 ok, it is better to give factorized motors a target too …
    to avoid scaling issues
    [Commands.ino, Motion.ino, TMC43x.ino]
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2013-11-21 ok, it seems to be easier if we configure the start signal in the motion routine
    who knows which other start signals we might need …
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2013-11-21 hmm the start signal should be generated in the right order …
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2013-11-22 this does not work in a very strange way …
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2013-11-26 ok, eith shorter targets we have problems to reach it in imt time …
    [SPI.ino]
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2013-12-02 ok, that is how we move twice as far as needed …
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2013-12-02 hmm, it seems that we know and register the events of the motors …
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2013-12-02 we must somehow know which motors to monitorand unify the start command
2013-12-02 ok, and we need to check if all motors reached their target …
2013-12-03 this should work …
    - fixed the interrupt registration
    - pos_comp now updated
    - some better logging
    [ArduinoClient.ino, Motion.ino, TMC43x.ino]
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2013-12-04 improved debugging and fixing some minor errors
    [ArduinoClient.ino, Commands.ino, Machine.py]
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2013-12-04 we seem to get the motion status right
    … which leads to no more motion … but there is nothing like free lunch …
2013-12-04 that's why we did not get any pos_comp event
    we had to read it in the start routine …
2013-12-04 ok it seems that this is how the motors really move …
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2013-12-04 solving symptoms,not problems …
    [ArduinoClient.ino, Commands.ino, Motion.ino]
2013-12-04 ok, setting pos_comp even to zero may help to avoid false triggers …
    [Motion.ino, TMC43x.ino]
2013-12-04 what is the problem??
    [TMC43x.ino]
2013-12-04 ok we have to track where we are
    to successfully know when to stop the motor
2013-12-04 we need a print queue
    since we have to deal with stoppin axis
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2013-12-05 ok and this is the more or less correct queue handling
    [motion-planning-tests.py]
2013-12-06 ok, just going slow enough is not enough … we have to ensure that it is stopping, not going slow
2013-12-06 but reversing is harder than thought …
    [motion-planning-tests.py]
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2013-12-06 it seems printing just got a whole lot easier with a queue
    … all the logic is in the queuen …
2013-12-06 uh oh - some tests were broken
    [motion-planning-tests.py]
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2013-12-09 it may help to include the correct functions …
    [helpers.py]
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2013-12-09 let's see is this is our waypoint logic
    since stopping works different than driving over …
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2013-12-09 dang, wasn't that the error anyway??
    [Motion.ino]
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2013-12-10 so we can see the problem better
    [ArduinoClient.ino, testprint.py]
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2013-12-10 it is better if we reset the arduino just to be on the sure side …
    [ArduinoClient.ino, Machine.py, Motion.ino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]
2013-12-10 ok, if we output the debug codes we can see the problem …
    [ArduinoClient.ino]
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2013-12-13 hmm, this is far too much output
    [EndstopTest.ino, SPI.ino]
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2013-12-17 why oh why doesn't it work??
    [EndstopTest.ino, SPI.ino]
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2013-12-18 damn damn damn buggydibugg
    [SPI.ino]
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2013-12-18 not too shabby for an error message
    [Machine.py, testprint.py]
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2013-12-19 there weere still some errosr until proper homing
    SPI readout problems
    motor speed config
    variable decleration
    [Commands.ino, TMC43x.ino]
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2013-12-19 reworking the todoes a bit
    [Machine.py]
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2014-01-08 not all the motion must happen in the interrupt routines
    it takes too long
    [Motion.ino]
2014-01-08 ok, there seems to be a problem …
    if we check for a motion if there is no running … but should work … but
    will not be useful - let's see
    [ArduinoClient.ino, Machine.py, Motion.ino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]
2014-01-08 does not move but at least this …
    … endstops seem to work correctly
    [Commands.ino]
2014-01-09 more info might hit to the problem …
    [ArduinoClient.ino, TMC43x.ino]
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2014-01-09 hmm, this was so definitvely not implemented correctly
    [Machine.py]
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2014-01-09 a clearer picture
    there are several problems and we will find them
    [Motion.ino, TMC43x.ino]
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2014-01-10 and an empty move ququ might be a major problem
    [Motion.ino]
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2014-01-10 catching already missed movement goals
    [Motion.ino, TMC43x.ino]
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2014-01-13 this seem to work
    so it was just the wrongly zeroed variable and additional println
    [ArduinoClient.ino, Motion.ino, TMC43x.ino]
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2014-01-15 error handling for the motion starting
    [Machine.py]
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2014-01-16 hmm, finishing the movement got an threading problem
    [Machine.py, Motion.ino, testprint.py]
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2014-01-20 not too much remains the same for the tmc5031
    [SPI.ino]
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2014-01-24 hmm, this was an import problem … solved … still a bit puzzling
    [helpers.py, t_bone_server.py]
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2014-01-27 trying to reduce restart problems … did not work
    [t_bone_server.py]
2014-01-27 if we do not understand a status command we do not crash … but still react puzzled
    [machine.py]
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2014-01-28 hmm the test prints are more global …
    [test-model.scad, test-model.stl]
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2014-01-29 hmm, you should get the JS from teh correct directory …
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2014-01-29 hmm, this timer did not work …
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2014-01-30 somehow the printing status was missing …
    [t_bone_server.py]
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2014-02-03 this should prevent the speed from getting zero … but this is just a fail safe method
    [printer.py]
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2014-02-03 this was the problem
    [printer.py]
2014-02-03 this was the problem II
    [printer.py]
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2014-02-05 at least partyl fixing the tests …
    [motion-planning-tests.py]
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2014-02-07 correct calculations and no computational cross talk?
    [motion-planning-tests.py]
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2014-02-07 checking if movement direction is translated correctly into movement types …
    [motion-planning-tests.py]
2014-02-07 even intensive testing shows that 'stop' and 'way' seems to be correct …
    [motion-planning-tests.py]
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2014-02-07 hmm, we even check if the correct motors move …
    [motion-planning-tests.py]
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2014-02-14 this fixes - in a way the worst things …
    [printer.py]
2014-02-18 hmm, the ration calculation is correct …
    ok, for different step settings we need a conversion factor . but this
    ain't a problem
    [motion-planning-tests.py, printer.py]
2014-02-18 we will need this different fixed/float encoding
    and aMax is now a float too …
    [TMC43x.ino, constants.h]
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2014-02-19 wrong float conversion …
    [ArduinoClient.ino, TMC43x.ino]
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2014-02-19 we explicitly set the spi clock div
    just to have it fixed - and to be able to change it later?!
    [TMC43x.ino]
2014-02-19 better logging for failed starts (slightly)
    [machine.py]
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2014-02-19 ok, at least we know the problem
    and it is not soo hard to solve - but no priority
    [gcode_interpreter.py]
2014-02-20 hmm, isn't taht the correct name? - at least arduino bothered me to do so
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2014-02-21 CS pins are now inverted
    and some precautions …
    [ArduinoClient.ino, SPI.ino, TMC4361.ino]
2014-02-21 x axis is inverted?!
2014-02-21 and we should tell the arduino which motor to invert …
    [ArduinoClient.ino, Commands.ino, TMC4361.ino]
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2014-02-21 we should have enought ime for a nice error message
    [Commands.ino]
2014-02-21 ok, you also have to change readout if you invert a motor
    and modified logging
    [ArduinoClient.ino, TMC4361.ino]
2014-02-21 ok let's cancel this problem for now …
    [Commands.ino]
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2014-02-24 Revert "in theory we no can set the current for both motors …"
    This reverts commit 08176f90ecb0a9f302c43cfb29a12188ee6565ba.
    [Commands.ino, TMC260.ino, TMC5041.ino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]
2014-02-24 Revert "Revert "in theory we no can set the current for both motors …""
    This reverts commit 42a375fe55192b4830f562fb6e6dc62f1aae090a.
    [Commands.ino, TMC260.ino, TMC5041.ino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]
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2014-02-24 the inversion should work for many motors as well …
    … and some corrections in using config vs axis …
    [printer.py]
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2014-02-25 adding default chopper value
    and fixing typos
    [TMC5041.ino, printer.py]
2014-02-25 the morots are adressed slightly different
    staying too late with TMC4361 and unsing wrong numbering in JSON
    [Commands.ino, TMC260.ino, TMC5041.ino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]
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2014-02-25 we should read homing followers only up to the 0
    and some minor errors
    [Commands.ino, machine.py]
2014-02-25 wrongly calculated the number of possible followers
    [Commands.ino]
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2014-02-27 this could be the homing
    … following is missing …
    [TMC4361.ino, TMC5041.ino, constants.h]
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2014-02-28 fixing the endstop config
    [Commands.ino, TMC5041.ino]
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2014-03-03 ok, this seems to be the correct motor speed …
2014-03-03 on the other hand the z axis is inverted …
2014-03-03 inverting TMC5041 is easy - acc. to tthe datasheet …
    [Commands.ino, TMC5041.ino]
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2014-03-03 if it is hard to program there might be an error in the data structure …
    [printer.py]
2014-03-03 there were still some errors in homing
    [Commands.ino, TMC5041.ino]
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2014-03-06 some new stuff to test …
    [big+fine.scad]
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2014-03-07 hmm, this sseems to work
    at least the movements are correctly added …
    [TMC4361.ino]
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2014-03-10 'nother test design …
    [little-complex.scad]
2014-03-10 motor current ocnfig does not work anymore??
    [ArduinoClient.ino, Commands.ino]
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2014-03-10 the deb sizing seems to be completely off
    previous value was not that bad … but still far too slow
    [ArduinoClient.ino]
2014-03-10 hmm y/z copy problems
    [TMC5041.ino, printer.py]
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2014-03-12 silly movement mistake …
    [ArduinoClient.ino, printer.py]
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2014-03-12 ok the basic interface won't be too hard
    [heater.py]
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2014-03-14 homing only - sketch too big - let's slim down
    [ArduinoClient.ino]
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2014-03-14 ok the config is now really fix!
    [json_config_file.py]
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2014-03-16 lots of little corrections
    [printer.py]
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2014-03-16 now correctly starting the heater
    [heater.py]
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2014-03-16 hmm switching btw GPIO & PWM does not work??
    [ArduinoClient.ino, beaglebone_helpers.py, heater.py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]
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2014-03-17 hmm there seems to be a problem with the heated bed??
    [printer.py]
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2014-03-17 ok, this homes x
    but y is broken??
    [ArduinoClient.ino, TMC4361.ino]
2014-03-17 debugging the 5041 alone
    because the sketch got too big
    [ArduinoClient.ino, TMC5041.ino]
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2014-03-19 what is wrong with the second PWM channel?
    [heater.py, printer.py]
2014-03-20 this pid seems to work failsafe enough
    [heater.py, printer.py]
2014-03-20 adding the missing gcodes to print
    [Commands.ino, gcode_interpreter.py, heater.py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]
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2014-03-23 dammit - wrong name
    [printer.py]
2014-03-24 this seems to fix most of the gcodes
    [gcode_interpreter.py]
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2014-03-24 you should write to the correct motors …
    [TMC5041.ino]
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2014-03-25 ok it seems that we now scale the extruder correctly
    [ArduinoClient.ino, Motion.ino, printer.py]
2014-03-25 is this a fix?
    or does it make it worse
    [ArduinoClient.ino, Commands.ino]
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2014-03-25 it seems that slower serial brings less problems
    [ArduinoClient.ino, Commands.ino, gcode_interpreter.py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]
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2014-03-25 wrong config changed for extruder current
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2014-03-26 hmm the homing prevention does not work reliably
    [gcode_interpreter.py]
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2014-03-26 this should prevent overshooting
    [printer.py]
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2014-03-27 hmm we have to introduce our own new pins file to avoid cyclic dependencies
    [beaglebone_helpers.py, printer.py]
2014-03-27 ok, but this gives problems with extrusion …
    [helpers.py]
2014-03-27 he said that there should not be too much acceleration & bow
    [Commands.ino]
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2014-03-31 starting the stallguard test
    … with something we already have …
    [ArduinoClient.ino, SPI.ino, StallGuardTest.ino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]
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2014-03-31 organizing the reset code
    [ArduinoClient.ino, TMC4361.ino]
2014-03-31 we have to wait until stall guard is read …
    [SGHome.ino]
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2014-04-01 in theory we can go there to crash into the mechanic …
    [SGHome.ino, StallGuardTest.ino, constants.h]
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2014-04-14 did not work with bitshift
    [TMC4361.ino]
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2014-04-15 at least crashing if acceleration is too high
    much better than wrap around
    [printer.py]
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2014-04-17 still some too high acceleration problems …
    [printer.py]
2014-04-17 reset everything to 0 after homing
    and some improved debugging
    [TMC4361.ino]
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2014-04-17 Some things I wonder about/changed
    Sense reesistors in Arduino Software wrong (thing not a problem since
    configured in BB)
    Motion.ino seems to be sth. wrong?!
    [ArduinoClient.ino, Motion.ino, constants.h]
2014-04-28 this should reduce most critical scale problems …
    [printer.py]
2014-04-28 this seems like a nice way to prevent overshoot errors
    ...
    [ArduinoClient.ino, Motion.ino, TMC4361.ino]
2014-04-28 it really bugged me that you cannot scale the extrusion
    [printer.py]
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2014-05-05 LED PIN assignment wrong
    correction of LED PINs
    [LEDS.py]
2014-05-27 schematic and board of last T-Bone version
    Added "CC-BY SA" text
    Some changes still have to be made..
    (Commented on interactive-matter projects site)
    [T_bone_REV_A_v0_99.brd, T_bone_REV_A_v0_99.sch]
2014-05-27 Breakout Boards, Holder Prusa I3, Silkscreen, BOM
    Added some other files from the project
    [BOM_v3.xlsx, Prusa T-Bone Holder.dxf, Prusa T-Bone Holder.skp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]
2014-07-08 this is the corrected, underestimating speed calculation …
    [printer.py]
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2014-07-10 ok, the length calculations were the problems of the movement …
    [printer.py]
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2014-07-11 hmm the double PWM channels do not work
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2014-07-11 we just wait for poscomp
    and blink for reading corrections
    [Motion.ino, TMC4361.ino]
2014-07-11 this was wrong
    we do not ocnsider different length
    [printer.py]
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2014-07-14 tests have shown tahat the formulas were wrong
    [motion-planning-tests.py, printer.py]
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2014-07-15 ok slight corrdctions lead to the correct acceleration
    [printer.py]
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2014-07-16 what a silly error
    [heater.py]
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2014-08-07 we want to test the buffer adding
    and reduced the buffer size - which seems to solve the problem …
    [ArduinoClient.ino, Commands.ino, Motion.ino]
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2014-09-16 uh oh, the JS was missing for the status
    and another templating variable …
    [t_bone_server.py]
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2014-11-18 Changed Sense Resistors, TMC2660 = 100mOhm, added SQRT_2 to TMC26XGenerator.cpp
    [tmc-260-shield.brd, tmc-260-shield.sch]
2014-12-02 Initial commit ================ Added ArduinoClient Folder --> Arduino software Added ArduinoLibraries Folder --> Libraries to run and compile Arduino software Added t_bone_server Folder --> Beagle B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
    [tmc-260-shield.brd, tmc-260-shield.sch]
2014-12-02 Changed folder structure
    Added Hardware schematics and board design for T-Bone
    Added Hardware schematics and board design for BBQ breakout board
    Added Hardware schematics for Programming board for T-Bone
    [BBQ.brd, BBQ.sch, T-Bone+Uart+Pulldown.sch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]
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2014-12-03 Wrong TMC26x library, changed to right one Added TMC2100-BOB files Added stallGuard test files for Arduino Added technical drawings for T-Bone Added plexiglas frame for Prusa I3
    [Prusa T-Bone Holder.dxf, Prusa T-Bone Holder.skp, T-Bone.dxf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]
2014-12-03 Restructured folder structure
    [BBQ.brd, BBQ.sch, BOM_v3.xlsx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]
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
